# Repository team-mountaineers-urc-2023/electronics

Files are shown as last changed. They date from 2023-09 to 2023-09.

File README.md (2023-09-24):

# Electronics
This repository contains diagrams of Wanderer's electrical systems as well as PCBs designed by the Electronics sub-team.

# Table of Contents
[Downloading the Repository](#downloading-the-repository)   
[Required Software](#required-software)  
[Repository Contents](#repository-contents)  

# Downloading the Repository
## Pre-Install: SSH Key
An ssh key for your current machine must be added to your Github account to clone our repositories.  
SSH keys are used for passwordless authentication.  
For more information see https://docs.github.com/en/authentication/connecting-to-github-with-ssh.

## Creating an SSh Key
`$ ssh-keygen`  
Keep the default file name, add a password if you'd like. 

## Adding the SSH Key to your Github account
Go to https://github.com/settings/keys and click "New SSH Key"  
The title can be anything.  
For Key, copy paste the output of `$ cat ~/.ssh/id_rsa.pub`

## Clone the workspace
Install git if not done so already with `$ sudo apt install git` then:  
`git clone git@github.com:team-mountaineers-urc-2023/electronics.git ~electronics`
* If this is your first time talking to Github on your machine, you will receive a warning saying authenticity cannot be established.  
	Type "yes" and hit enter.

# Required Software
Block diagrams and schematics can be viewed using any PDF viewer.
All PCBs were designed using KiCad 7.0. The most recent version of the software can be downloaded at https://www.kicad.org/download/.

# Repository Contents

## System Schematics

Main Electronics Box Diagram

Manipulator Electronics Diagram

Science Electronics Diagram

## PCB Files

Battery Monitor v1.2

Payload PCB v3.1

Power Distribution Board

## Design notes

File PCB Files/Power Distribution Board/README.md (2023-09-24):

# Power Distribution Board

## Overview
The Power Distribution Board includes DC/DC converters used to step down the battery power to the necessary voltages needed throughout the rover. It can be populated with up to three 40 or 60W Traco Power DC/DC converters as well as two 20W regulators. It also includes integrated emergency stop circuitry and two pass-through power rails.

## Features
- 2-layer board
- Supports up to four batteries powering DC/DC converters
- Allows up to three 40W or 60W regulators
- Includes up to two 20W regulators
- Two pass-through voltage rails allowing unregulated power directly from batteries
- In-rush current limiters on drive motor connections
- Connectors have selectable outputs - jumpers determine which regulator they are attached to
- E-stop bypass allows the computer to remain powered when the emergency stop is used

## Contributors
- Scott Harper
- Conner Castle
- Yu Gu

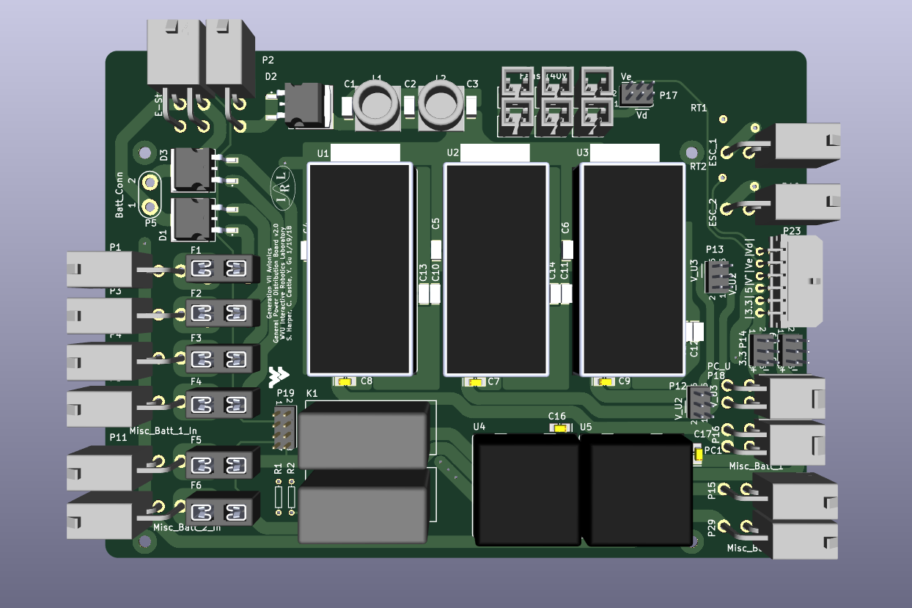
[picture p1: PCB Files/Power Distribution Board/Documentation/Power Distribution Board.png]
Picture of power distribution board


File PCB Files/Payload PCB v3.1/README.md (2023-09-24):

# Payload PCB v3.1

## Overview
The Payload PCB is used to control the electronics on the manipulator and the science payload. It can control up to eight DC motors and twelve servos. It also includes the hardware necessary for CAN bus communication, extra I/O connectors, payload select signals, and a USB2CAN converter.

## Features
- 4-layer board
- Raspberry Pi Pico microcontroller
- 4 DRV8874 H-bridge motor driver breakout boards capable of controlling 12V motors
- 2 TB6612FNG motor driver breakout boards that can each control two 12V motors or one stepper motor
- Capable of controlling up to twelve servo motors with selectable power output
- Hardware for CAN bus communication
- Optional place to put a 16th brick 12V regulator to power the board and payload motors
- 17 I/O connectors with GPIO, PWM, and/or analog input capabilities
- Payload select pins and LEDS to indicate which payload is plugged in
- Integrated USB2CAN converter which allows the computer to connect to the CAN bus using a USB connection
- Reverse polarity protection

## Contributors
- [Zach Waddell](https://github.com/zmw0006)

- [Ronald Butts](https://github.com/rmb0034)

- [Kendra Gillo](https://github.com/kgillo)

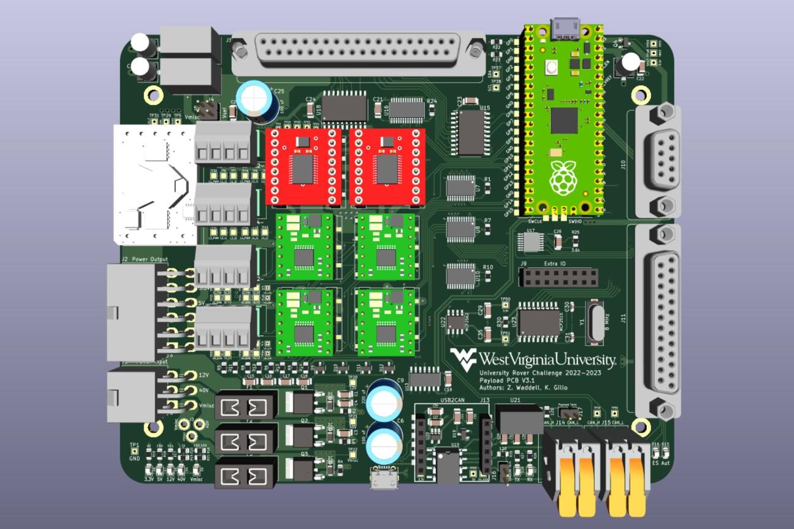
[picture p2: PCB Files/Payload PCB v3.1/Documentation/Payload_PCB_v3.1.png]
Picture of Payload PCB


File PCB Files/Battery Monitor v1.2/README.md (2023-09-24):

# Battery Monitor v1.2

## Overview
The battery monitor was designed for the 2023 rover to monitor its battery usage. The PCB features shunt resistors to measure the current draw from up to four batteries. It can communicate status using an LCD screen or over the rover's CAN bus.

## Features
- 4-layer board
- Raspberry Pi Pico microcontroller
- Measures battery voltage and current using shunt resistors combined with LTC4151 ICs
- Embedded emergency stop circuitry
- Ideal diode circuits to connect batteries in parallel
- Control for an external LCD screen and an LED strip
- Hardware for CAN bus communication
- Reverse polarity protection

## Contributors
- [Kendra Gillo](https://github.com/kgillo)

- [Zach Waddell](https://github.com/zmw0006)

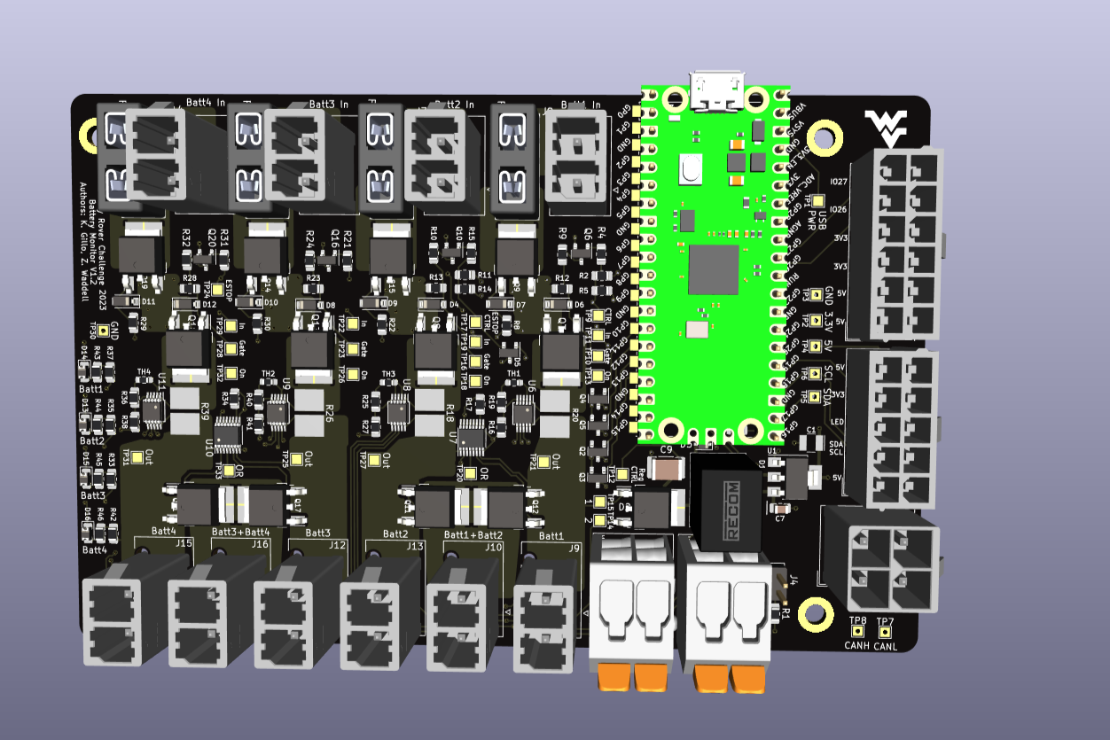
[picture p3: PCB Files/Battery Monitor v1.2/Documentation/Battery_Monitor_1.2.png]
Picture of Battery Monitor PCB


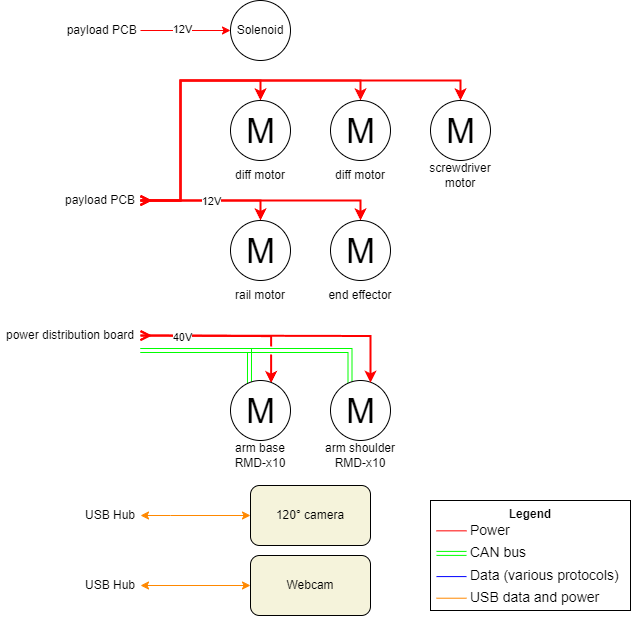
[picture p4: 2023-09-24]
System Schematics/Manipulator Electronics Diagram.png

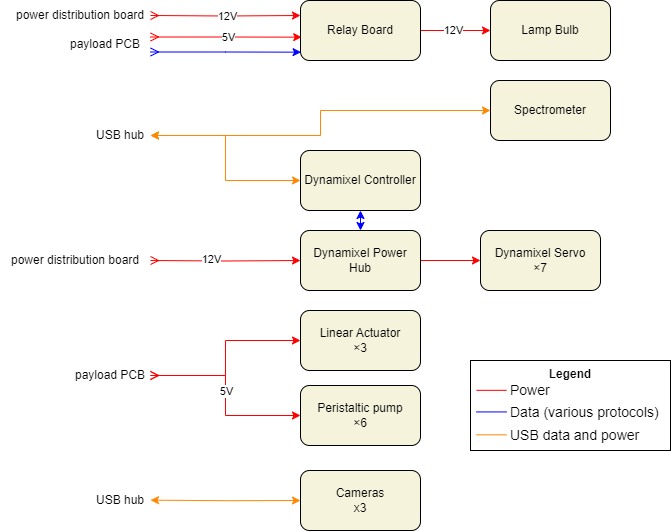
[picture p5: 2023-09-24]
System Schematics/Science Electronics Diagram.png

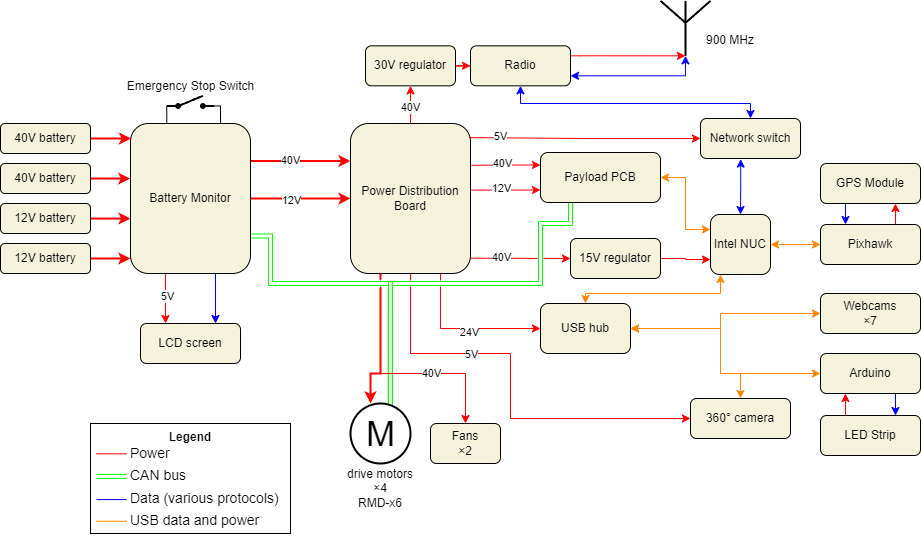
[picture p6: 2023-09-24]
System Schematics/Main Electronics Box Diagram.png

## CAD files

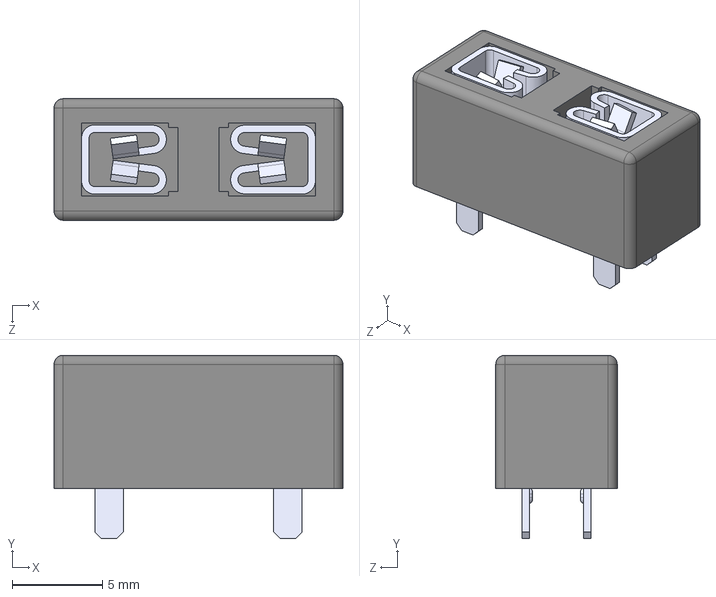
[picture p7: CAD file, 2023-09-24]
PCB Files/Battery Monitor v1.2/3D Models/3568.step
16.0 x 10.2 x 6.73 mm

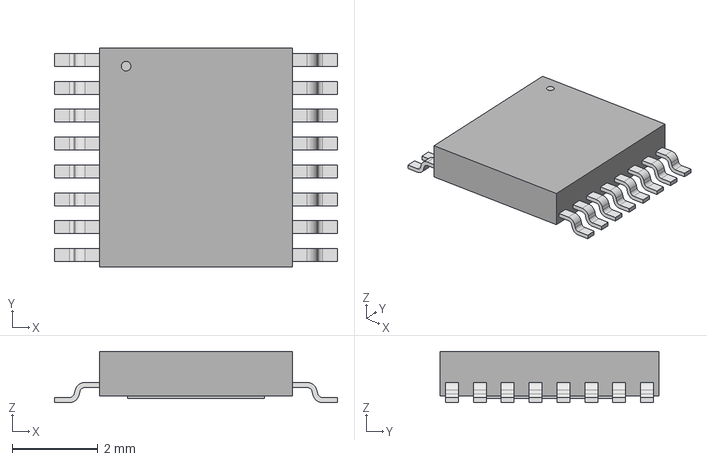
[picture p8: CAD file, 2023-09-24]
PCB Files/Payload PCB v3.1/3D Models/HTSSOP16_STM.step
6.60 x 5.11 x 1.20 mm

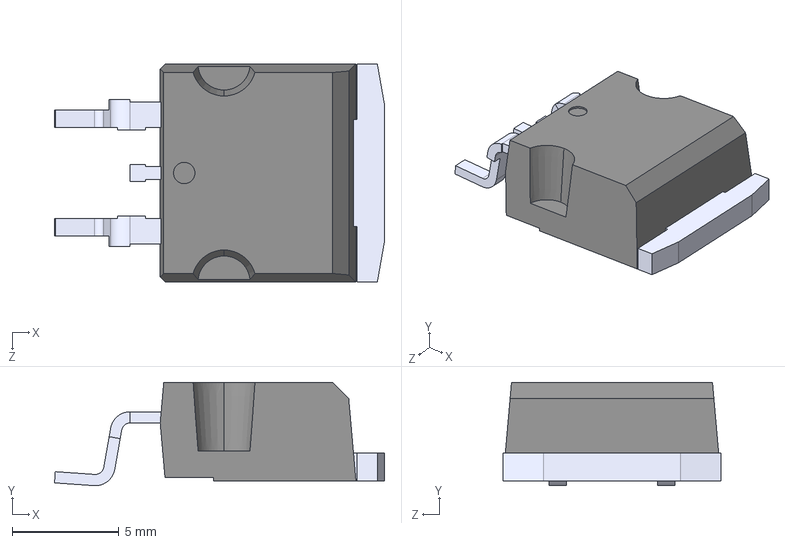
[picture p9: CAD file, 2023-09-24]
PCB Files/Power Distribution Board/3D Models/MBRB20200CTT4G.STEP
15.4 x 4.83 x 10.2 mm

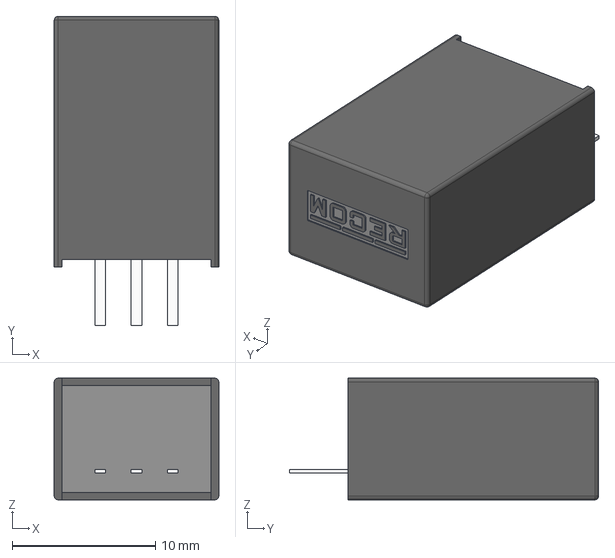
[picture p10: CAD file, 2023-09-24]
PCB Files/Battery Monitor v1.2/3D Models/R-78HB5.0-0.5.step
11.5 x 21.6 x 8.50 mm

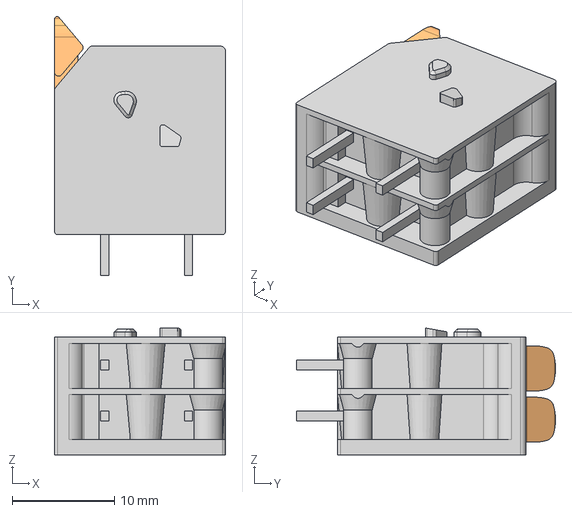
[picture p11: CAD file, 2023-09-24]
PCB Files/Battery Monitor v1.2/3D Models/2604-3102.stp
16.7 x 25.3 x 12.4 mm

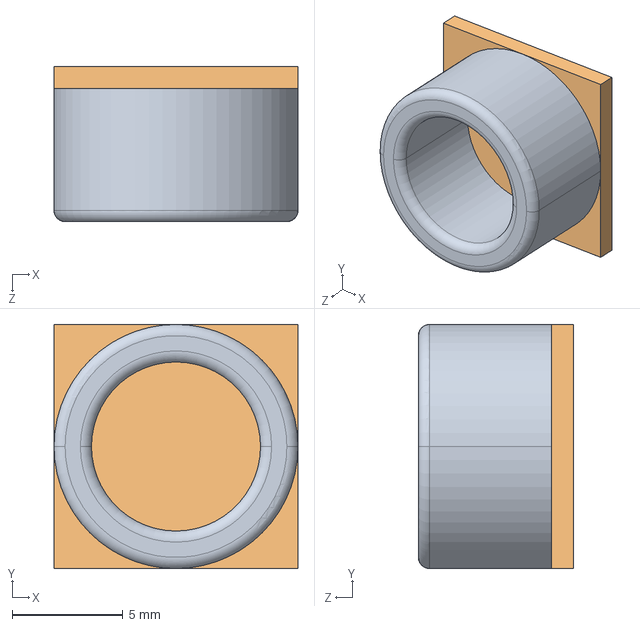
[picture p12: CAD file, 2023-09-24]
PCB Files/Power Distribution Board/3D Models/L1.STEP
11.0 x 11.0 x 7.00 mm
Cylinder.STEP
Extruded_14.STEP

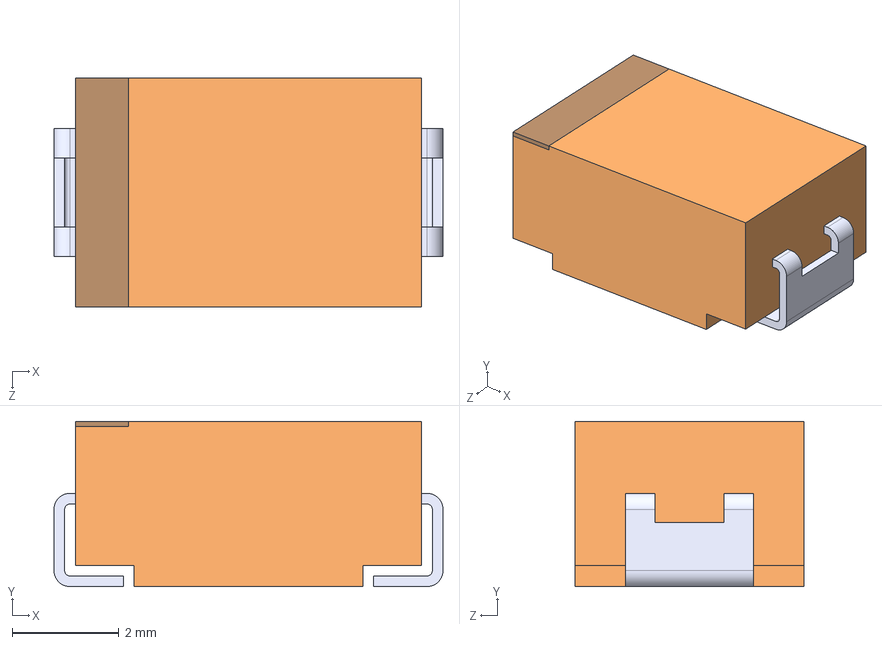
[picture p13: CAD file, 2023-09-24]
PCB Files/Battery Monitor v1.2/3D Models/2917.STEP
7.30 x 3.10 x 4.30 mm

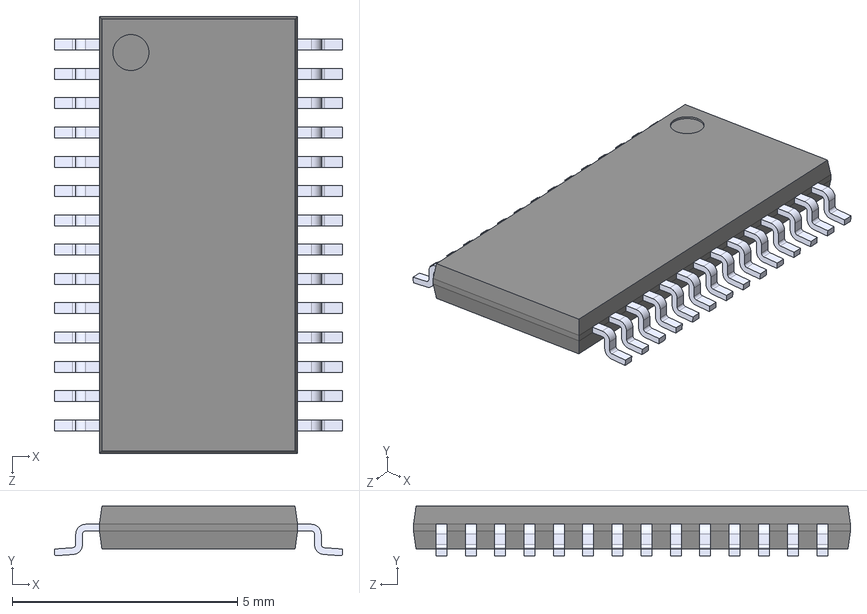
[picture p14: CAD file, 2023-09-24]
PCB Files/Payload PCB v3.1/3D Models/PCA9685PW_118.step
6.40 x 1.10 x 9.70 mm

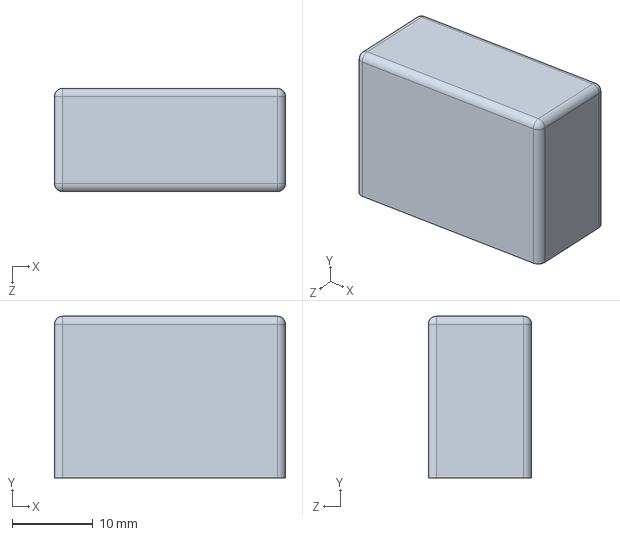
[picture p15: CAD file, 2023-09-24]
PCB Files/Power Distribution Board/3D Models/Relay.STEP
28.6 x 20.0 x 12.8 mm

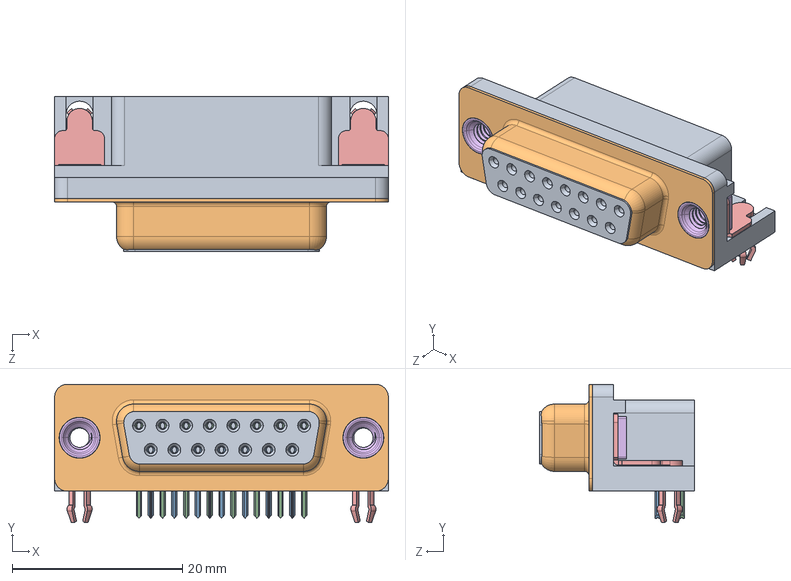
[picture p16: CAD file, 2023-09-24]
PCB Files/Payload PCB v3.1/3D Models/622-015-260-042 - EDAC D-Sub Connector.STEP
39.2 x 16.3 x 18.2 mm
622 Housing_15 Socket
622 Shell_15 Socket
622 Socket Bottom x 7
622 Contact Top x 8
622 4 Prong Board Lock x 2
622 4-40 Threaded Rivet x 2

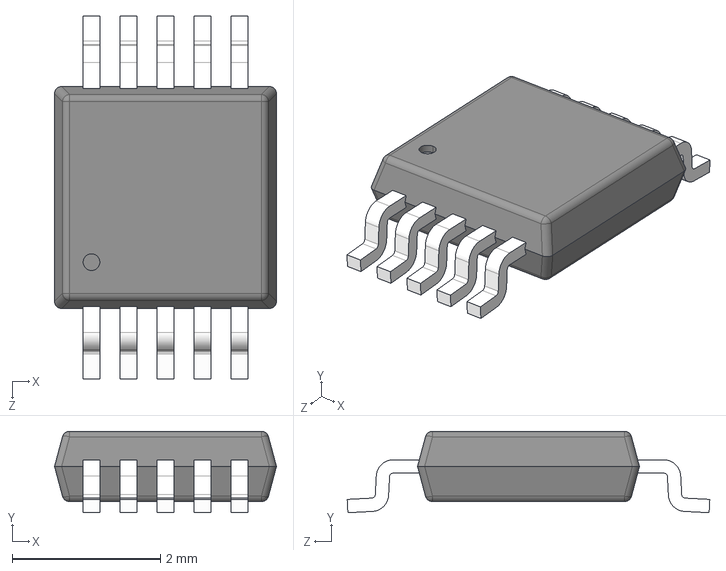
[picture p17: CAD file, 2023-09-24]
PCB Files/Battery Monitor v1.2/3D Models/MSOP-10.STEP
3.00 x 1.10 x 4.90 mm

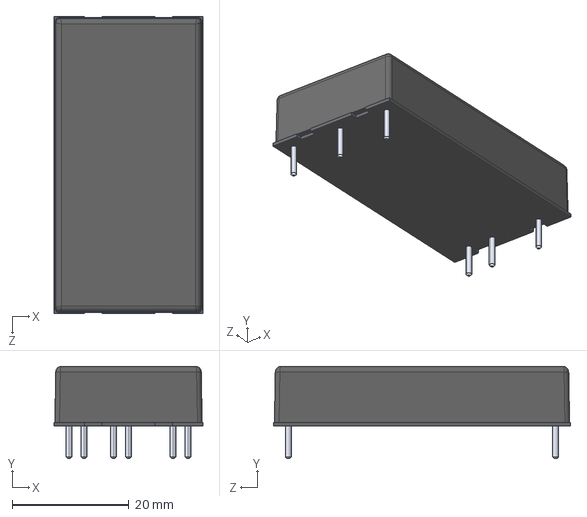
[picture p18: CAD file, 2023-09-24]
PCB Files/Power Distribution Board/3D Models/TEN 60-4813N.STEP
25.4 x 15.8 x 50.8 mm

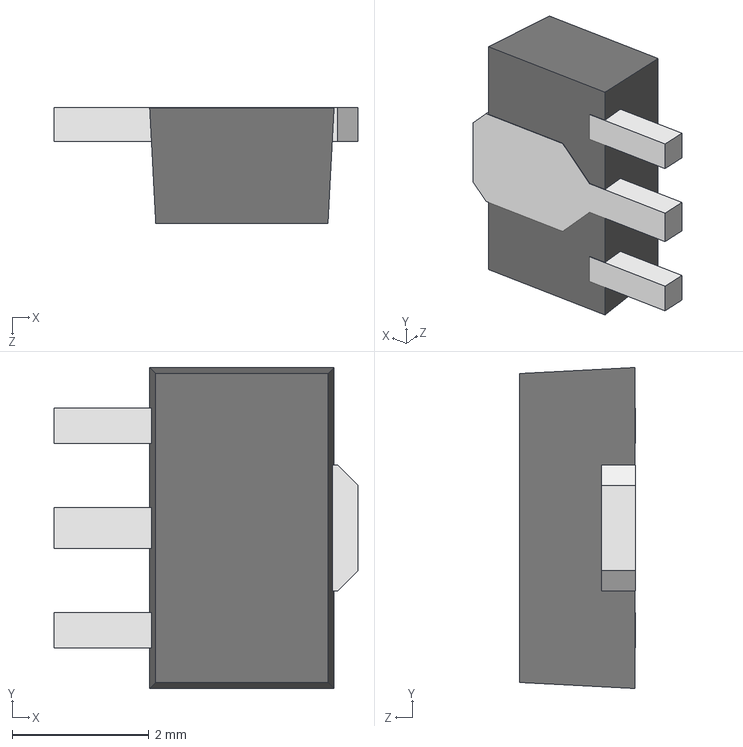
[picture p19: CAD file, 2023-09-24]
PCB Files/Battery Monitor v1.2/3D Models/TO-243AA.STEP
4.45 x 4.70 x 1.70 mm

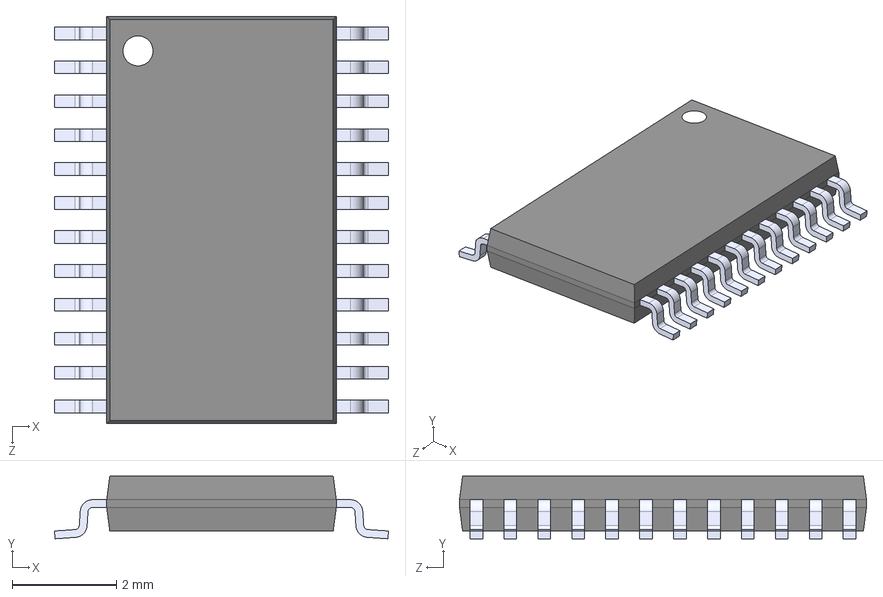
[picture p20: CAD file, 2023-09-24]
PCB Files/Payload PCB v3.1/3D Models/PCA9555PWR.step
6.40 x 1.20 x 7.80 mm

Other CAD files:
PCB Files/Power Distribution Board/3D Models/T491A474K025AT.STEP
PCB Files/Battery Monitor v1.2/3D Models/Molex 2x2.STEP
PCB Files/Payload PCB v3.1/3D Models/L77SDEH09SOL2RM8.stp
PCB Files/Battery Monitor v1.2/3D Models/VLS3015CX-680M-1.STEP
PCB Files/Battery Monitor v1.2/3D Models/039281103.stp
PCB Files/Battery Monitor v1.2/3D Models/039281123.stp
PCB Files/Battery Monitor v1.2/3D Models/768290102.step
PCB Files/Battery Monitor v1.2/3D Models/768290104.step
PCB Files/Battery Monitor v1.2/3D Models/Molex 2x1.STEP
PCB Files/Payload PCB v3.1/3D Models/050362296.stp
PCB Files/Payload PCB v3.1/3D Models/1050170001.stp
PCB Files/Payload PCB v3.1/3D Models/173010342_STP_173010342_rev1.stp
PCB Files/Payload PCB v3.1/3D Models/2604-1102.stp
PCB Files/Payload PCB v3.1/3D Models/2604-3104.stp
PCB Files/Payload PCB v3.1/3D Models/39301062.STEP
PCB Files/Payload PCB v3.1/3D Models/39301062.stp
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

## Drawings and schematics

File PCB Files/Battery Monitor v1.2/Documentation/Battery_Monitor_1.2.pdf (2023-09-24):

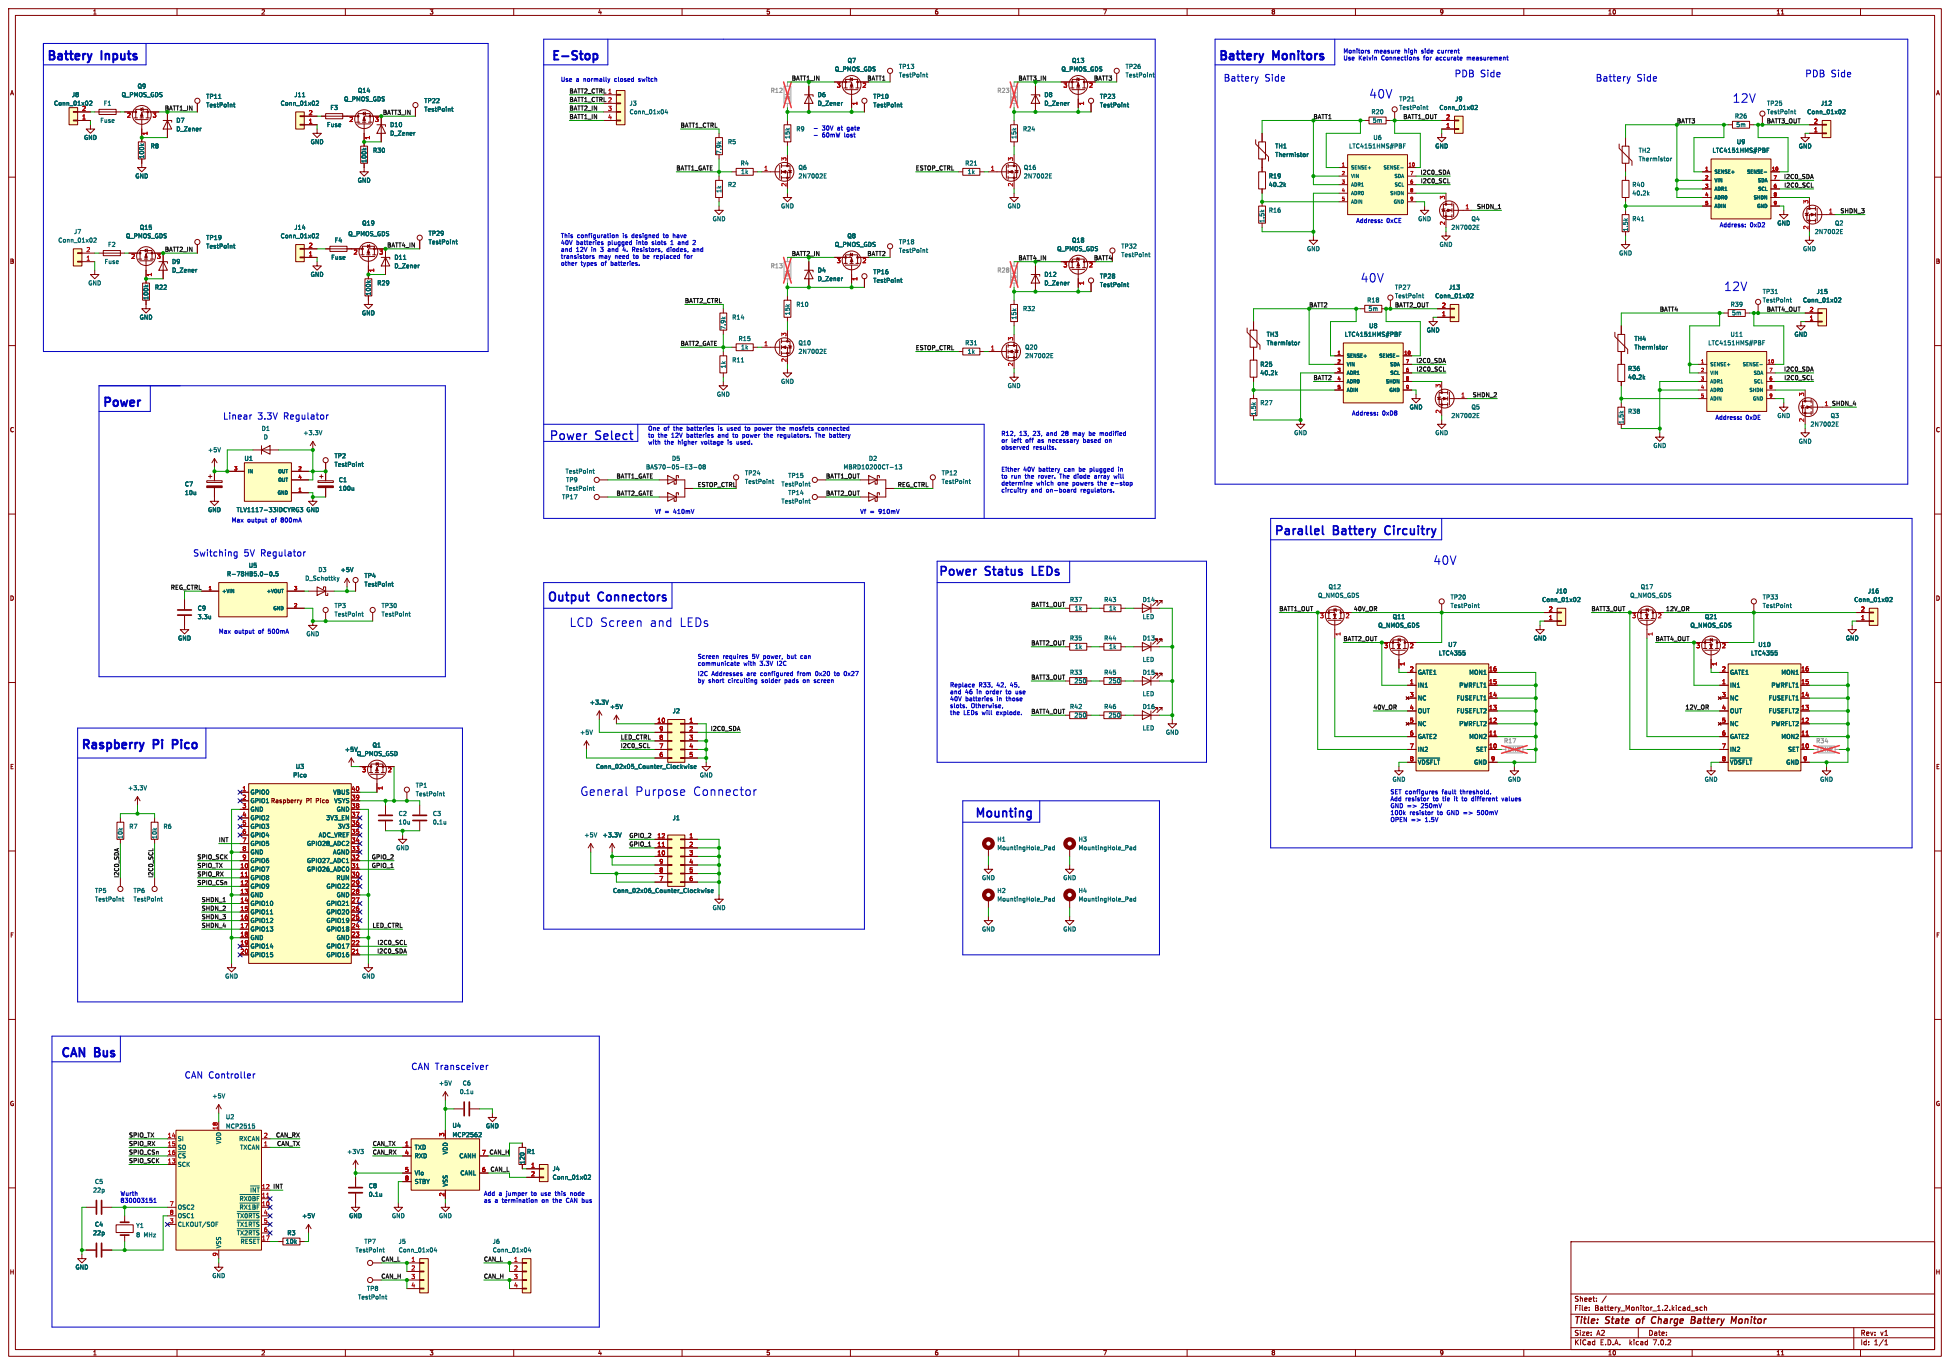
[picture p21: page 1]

PDB Side Battery Side

- 60mW lost Raspberry Pi Pico

R12, 13, 23, and 28 may be modified
or left off as necessary based on

Replace R33, 42, 45, and 46 in order to use

slots. Otherwise,
the LEDs will explode.

3 RXD 4 Vio 5 CANL 6 CANH 7 STBY 8 U4 MCP2562

3 RXD 4 Vio 5 CANL 6 CANH 7 STBY 8 GND

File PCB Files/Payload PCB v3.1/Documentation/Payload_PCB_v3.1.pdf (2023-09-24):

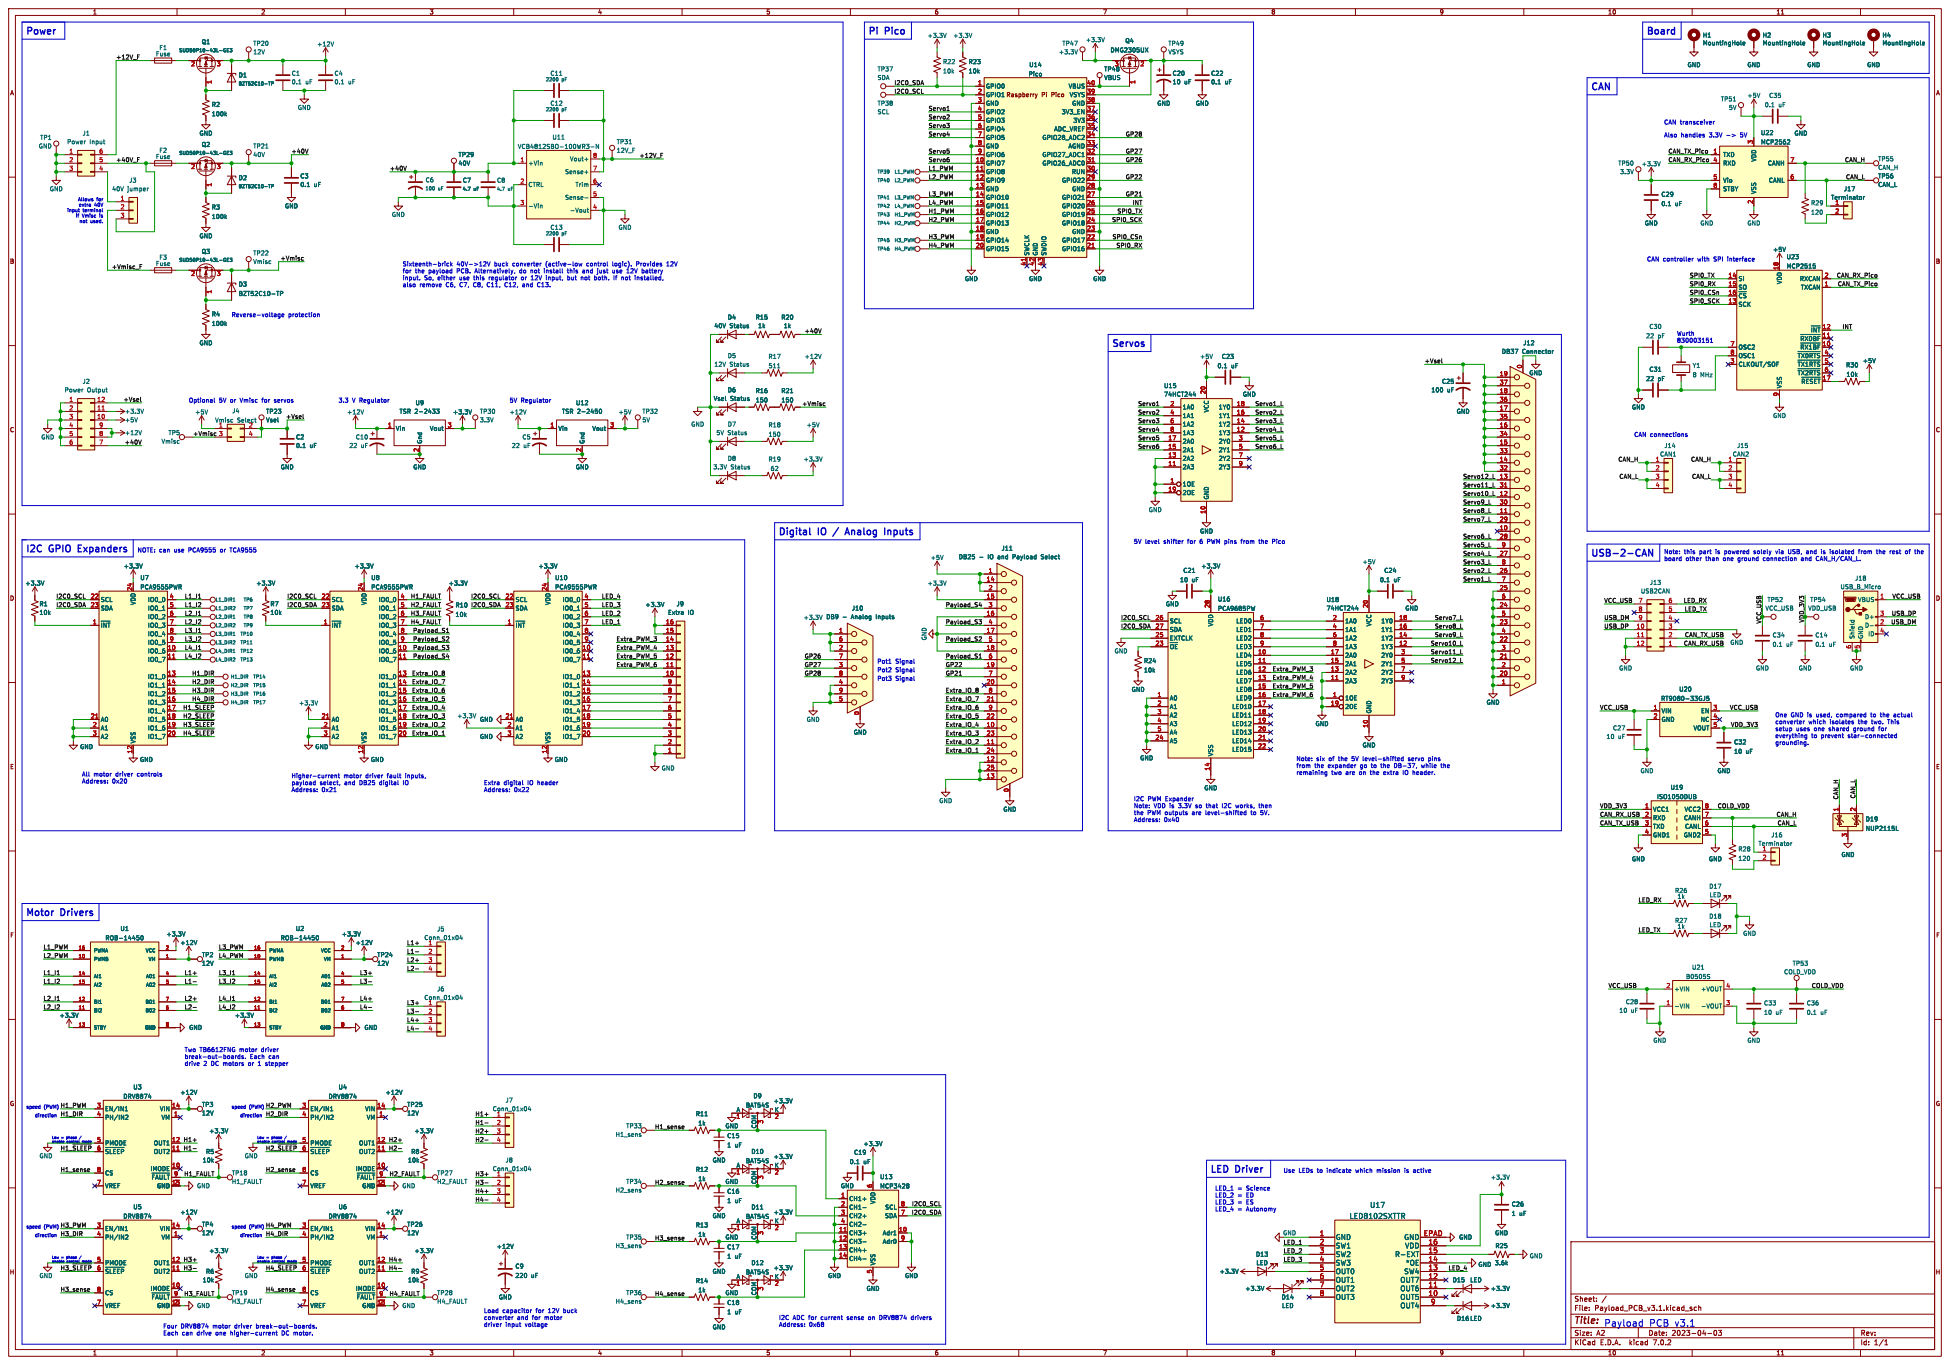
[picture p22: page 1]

input terminal
if Vmisc is not used.

J11 DB25 - IO and Payload Select 0

Digital IO / Analog Inputs

J11 DB25 - IO and Payload Select

All motor driver controls Address: 0x20

I2C PWM Expander Note: VDD is 3.3V so that I2C works, then

speed (PWM) speed (PWM) direction

6 SDA 7 SCL 8 Adr0 9 GNDGND GND

I2C ADC for current sense on DRV8874 drivers Address: 0x68

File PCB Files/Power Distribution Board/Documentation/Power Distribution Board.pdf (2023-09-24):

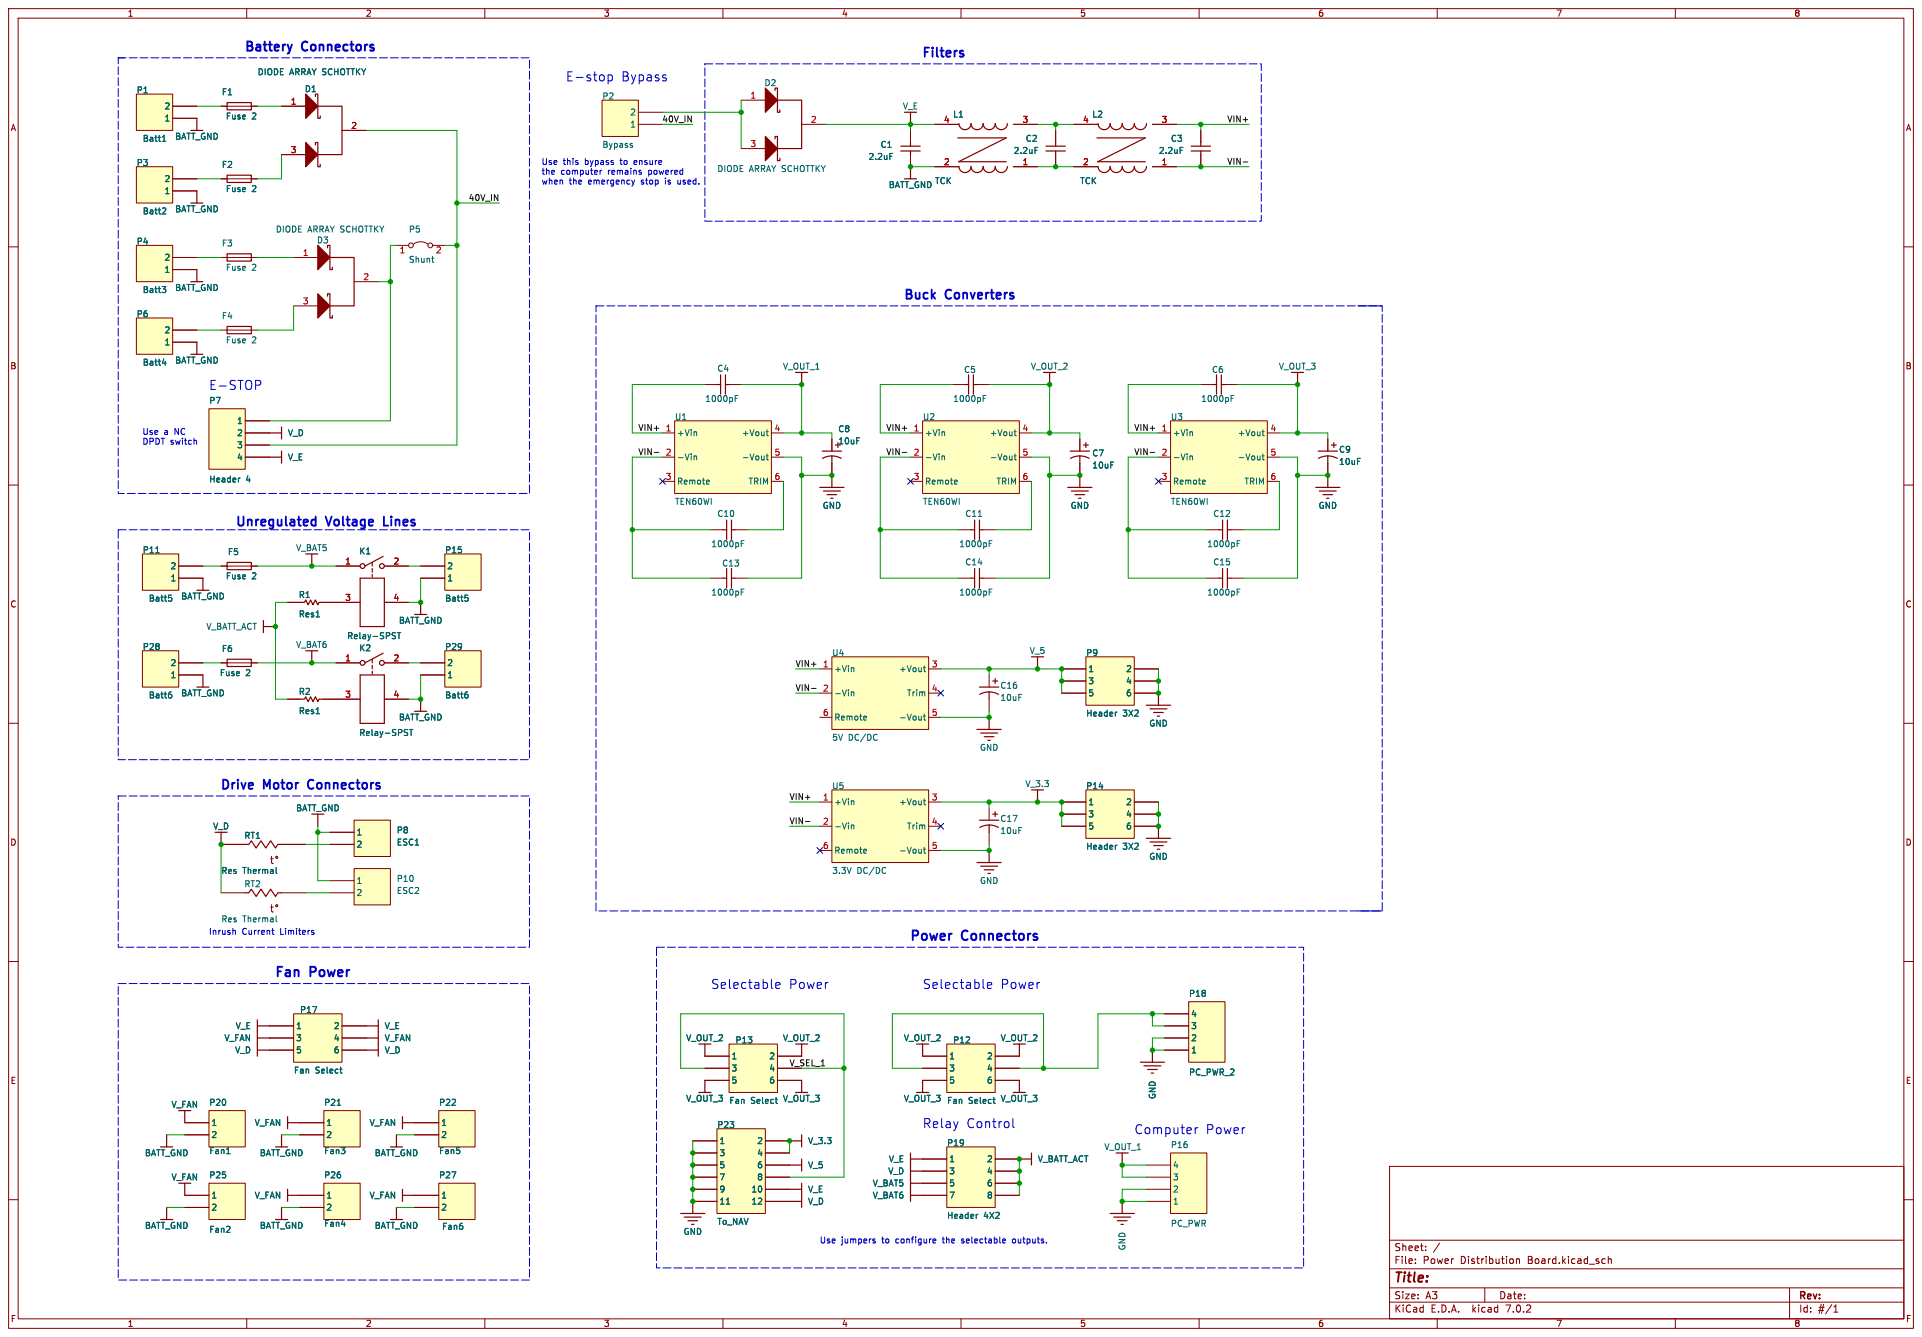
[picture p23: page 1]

Use this bypass to ensure

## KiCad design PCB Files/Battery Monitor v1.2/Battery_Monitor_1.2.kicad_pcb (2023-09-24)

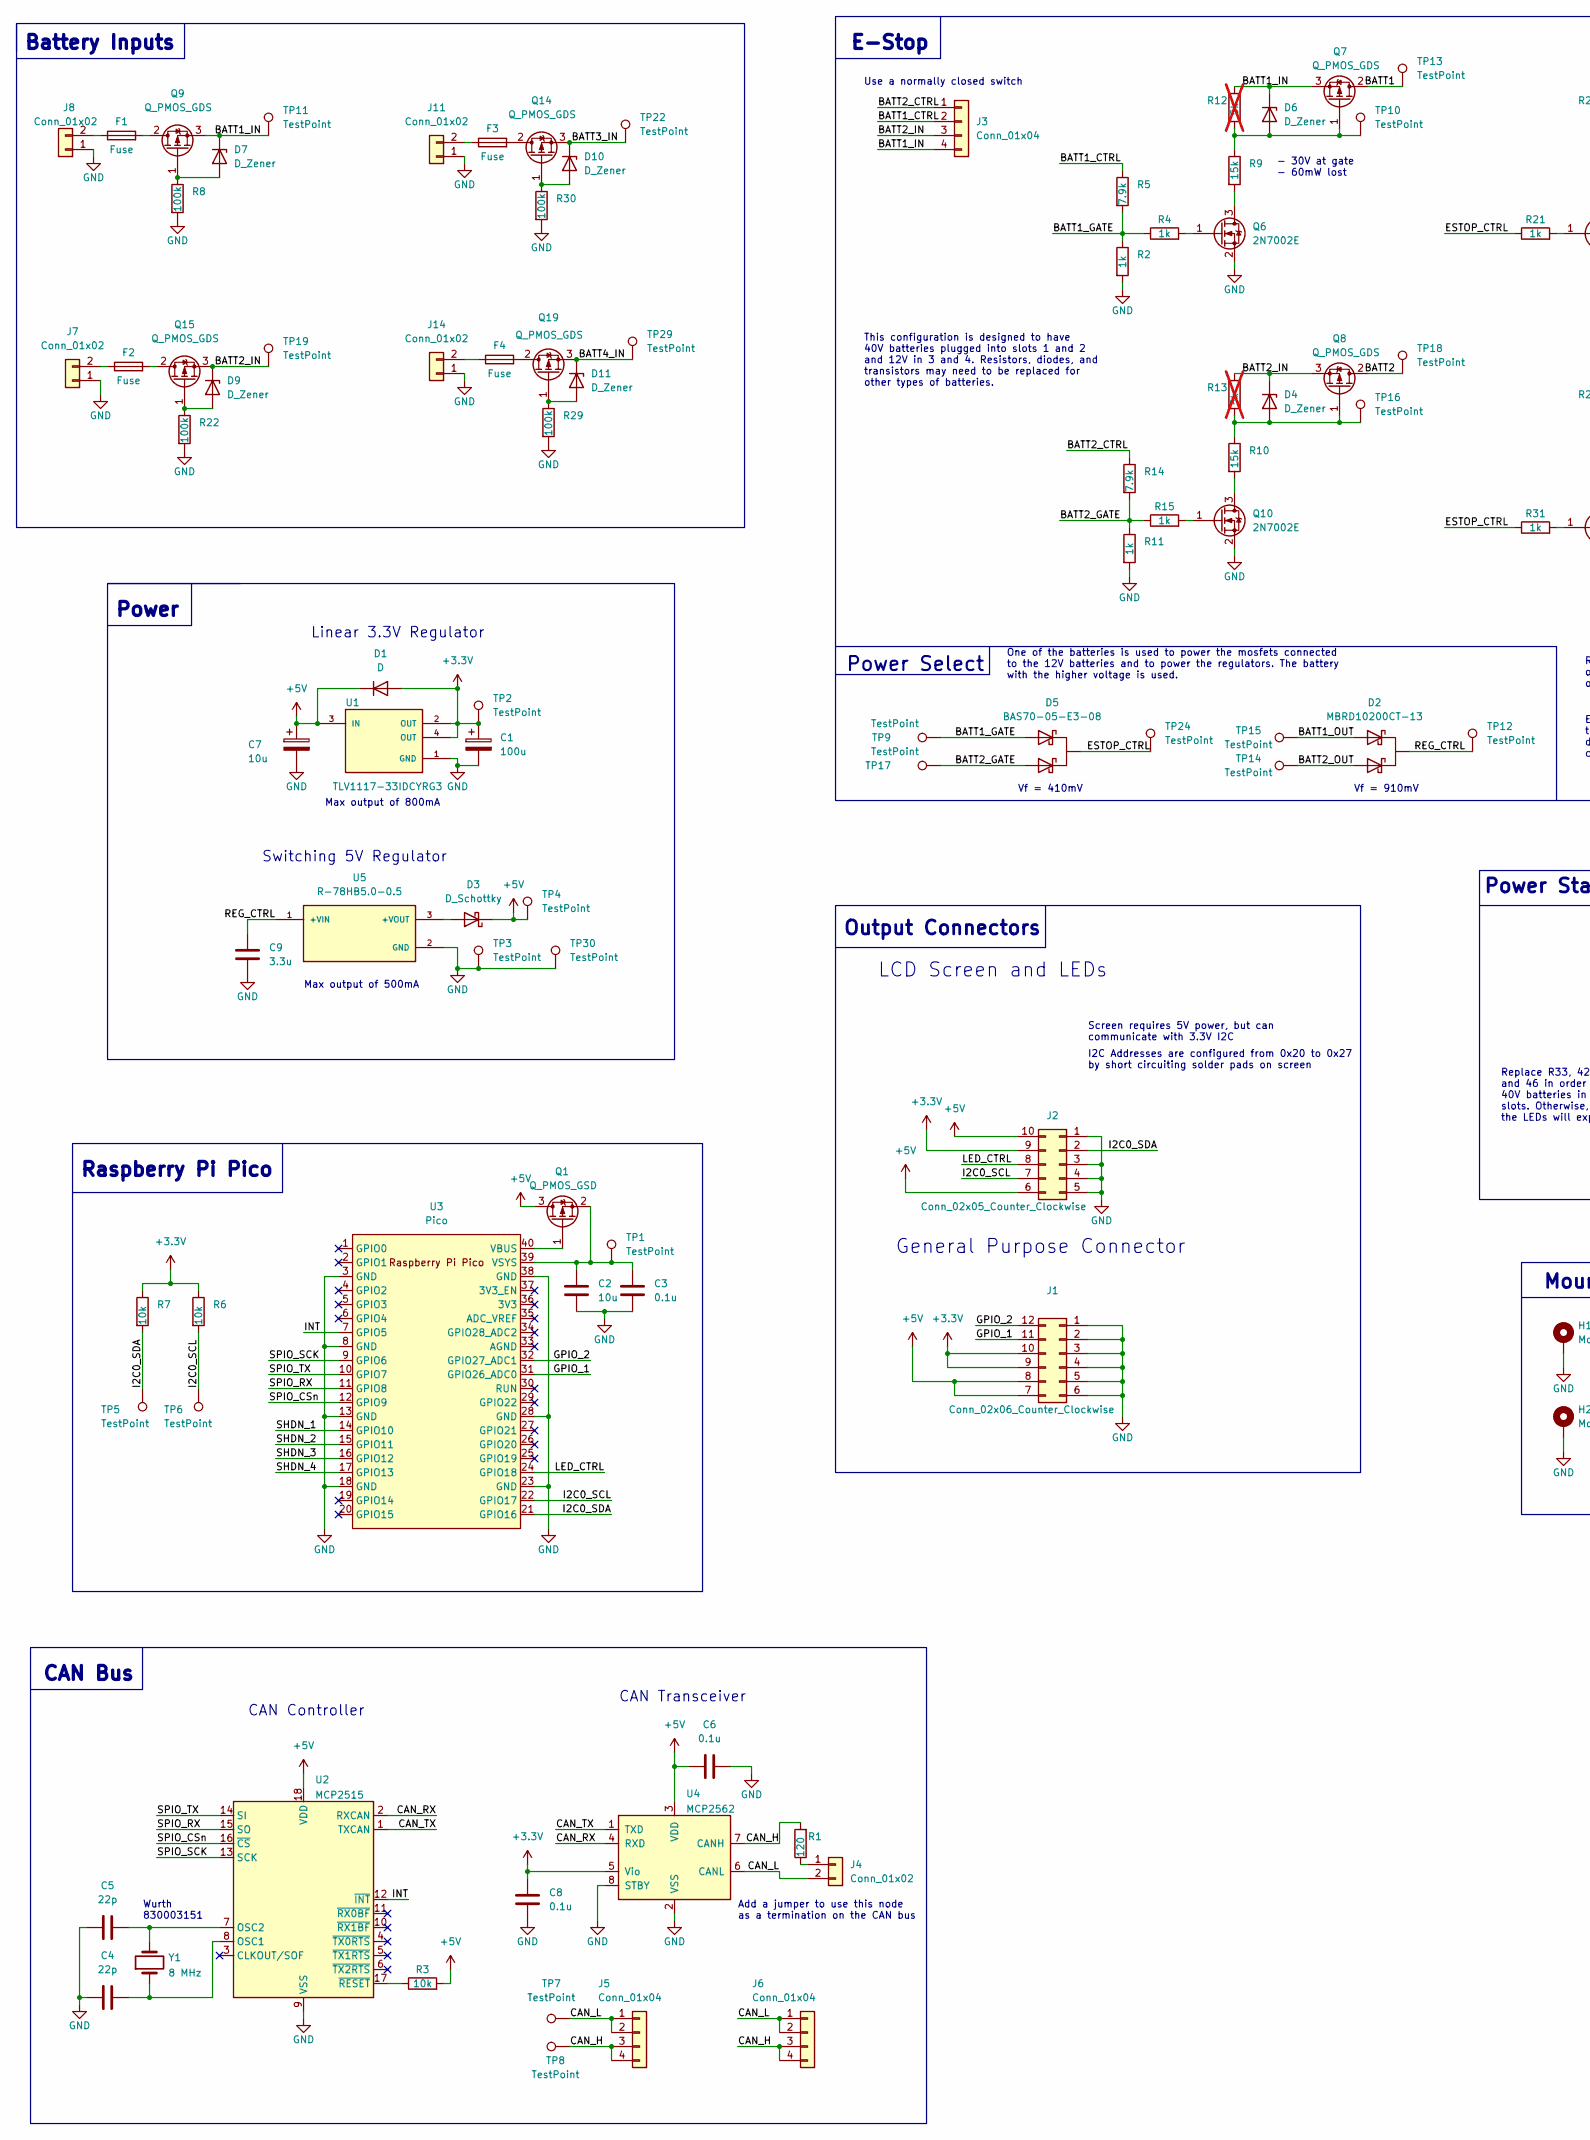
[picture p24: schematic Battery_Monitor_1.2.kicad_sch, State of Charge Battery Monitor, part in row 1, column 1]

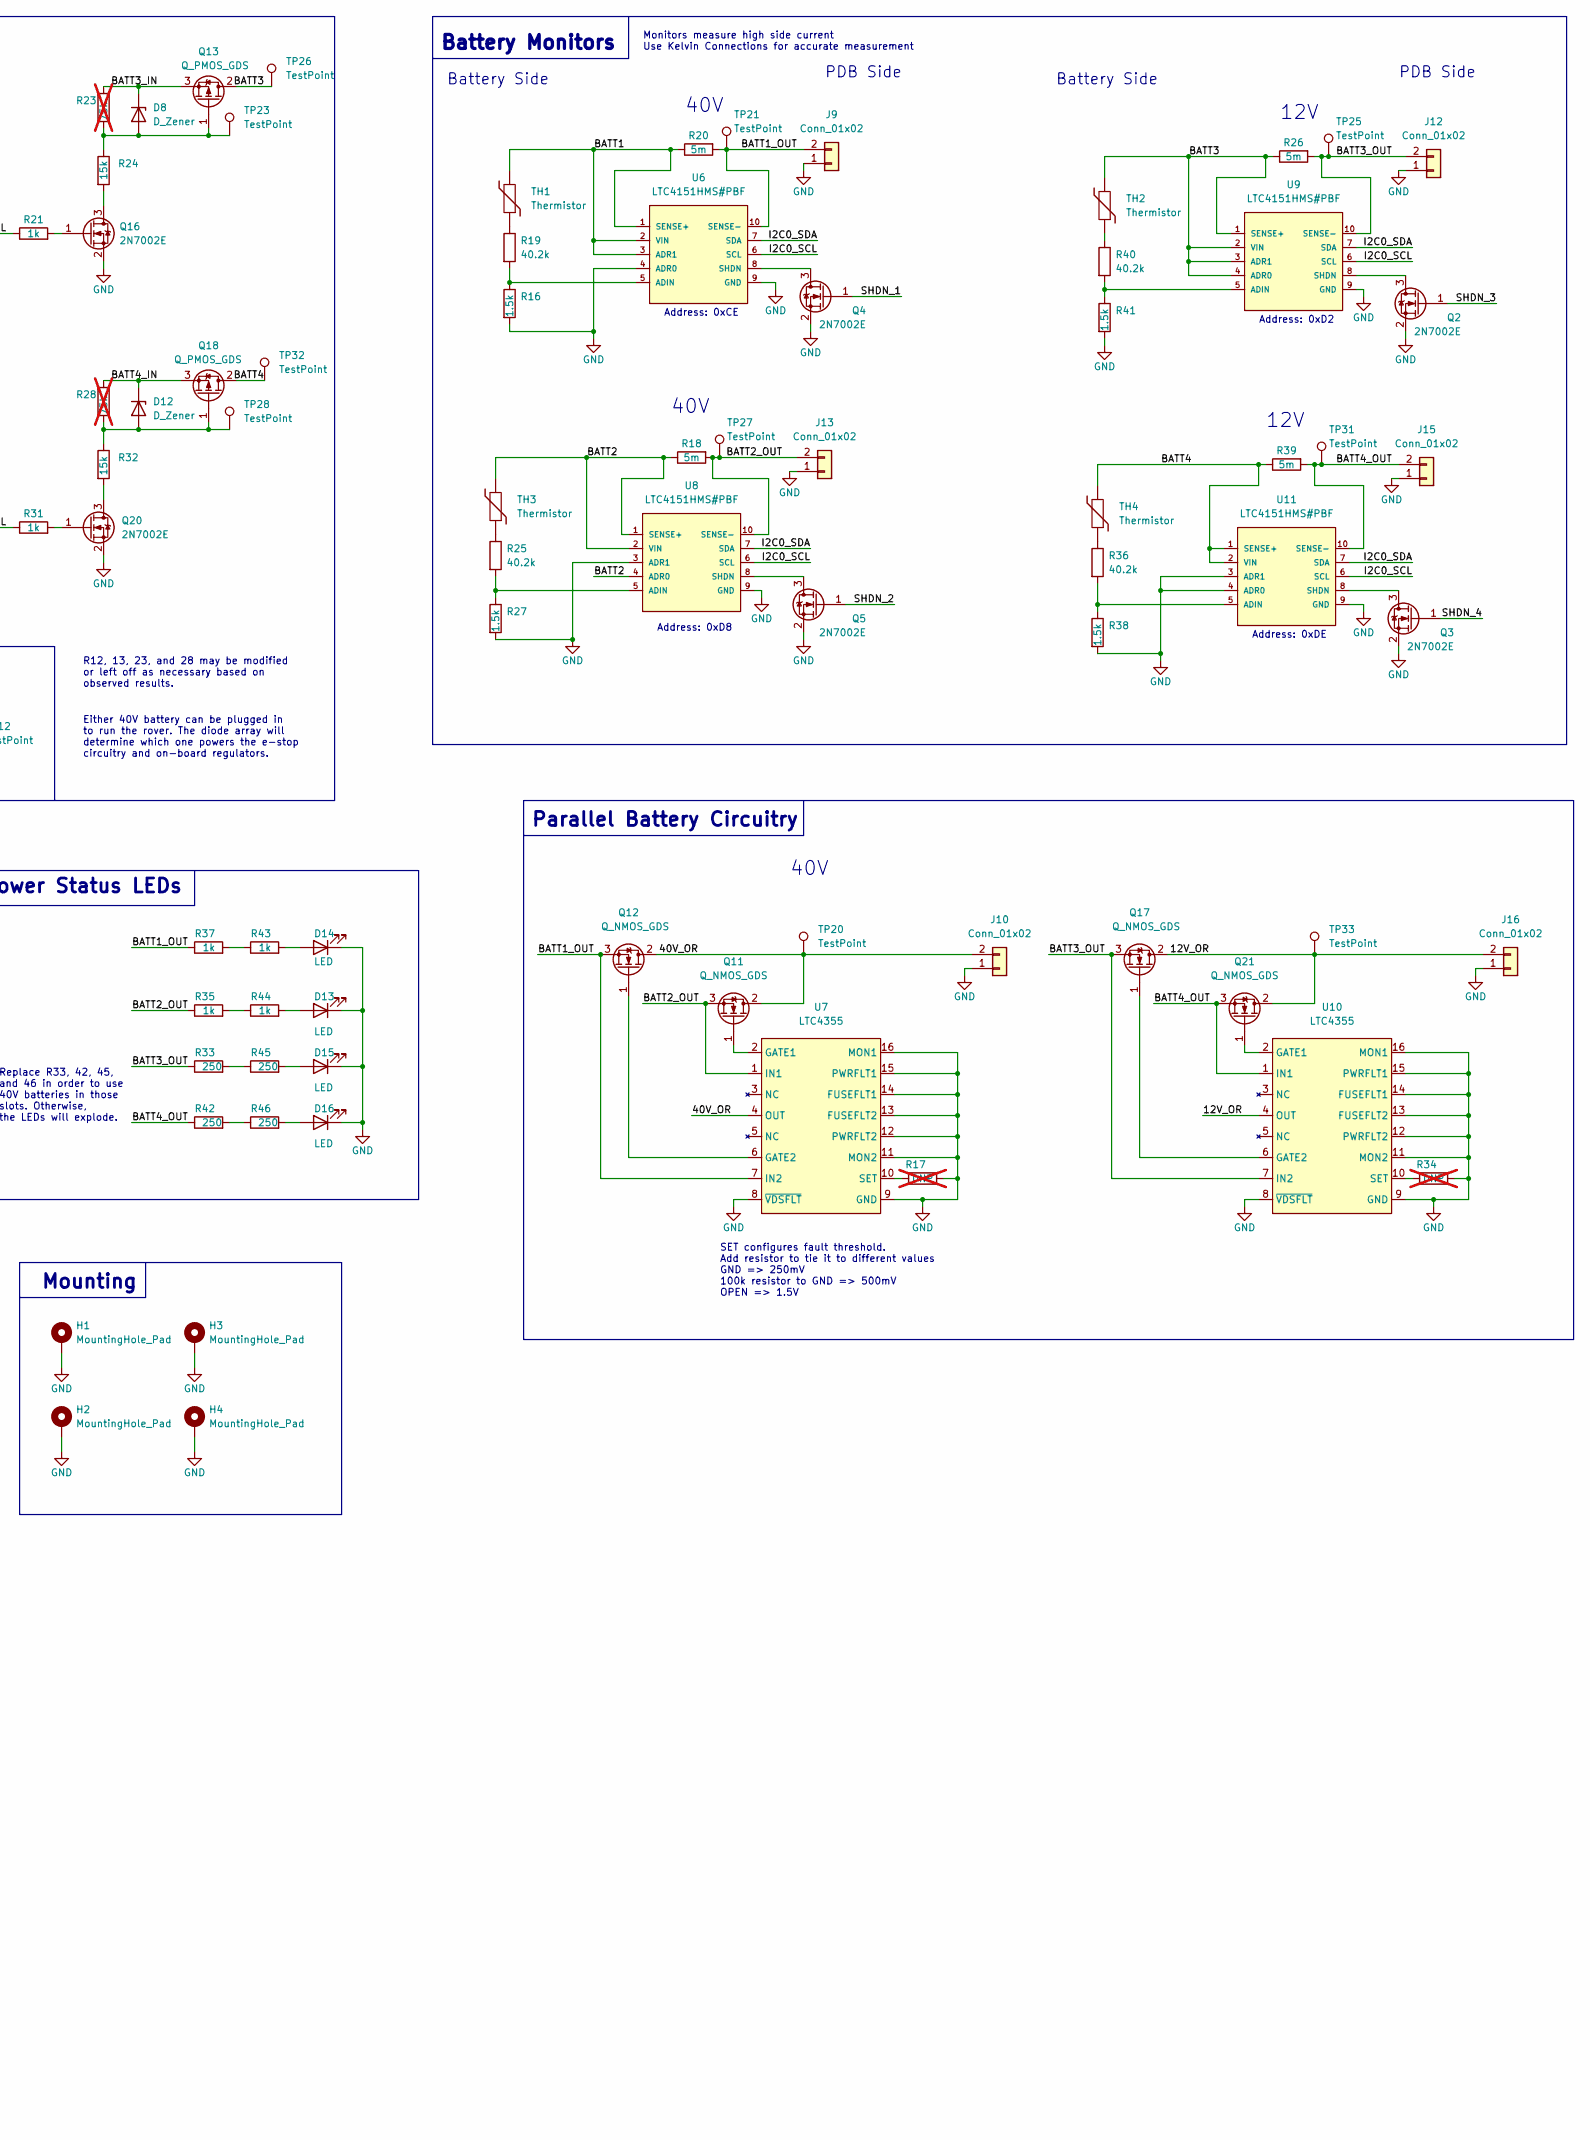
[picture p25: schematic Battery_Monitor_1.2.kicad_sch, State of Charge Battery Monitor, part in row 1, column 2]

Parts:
C1: 100u; 1411 (3528 Metric)
C2, C7: 10u; C_0805_2012Metric_Pad1.18x1.45mm_HandSolder
C3: 0.1u; C_1206_3216Metric_Pad1.33x1.80mm_HandSolder
C4, C5: 22p; C_0603_1608Metric_Pad1.08x0.95mm_HandSolder
C6, C8: 0.1u; C_1206_3216Metric_Pad1.33x1.80mm_HandSolder; MANUFACTURER_PART_NUMBER 1206B104J500CT
C9: 3.3u; C_1812_4532Metric_Pad1.57x3.40mm_HandSolder
D1: D; SOD123FL3; MANUFACTURER_PART_NUMBER GS1001FL_R1_00001
D2: MBRD10200CT-13; TO-252-2; MANUFACTURER_PART_NUMBER MBRD10200CT-13
D3: D_Schottky; D_SOD-323; MANUFACTURER_PART_NUMBER CUS08F30,H3F
D4, D6, D7, D8, D9, D10, D11, D12: D_Zener; D_SOD-123; MANUFACTURER_PART_NUMBER BZT52C10-TP
D5: BAS70-05-E3-08; SOT-23; MANUFACTURER_PART_NUMBER BAS70-05-E3-08
D13, D14, D15, D16: LED; D_0805_2012Metric_Pad1.15x1.40mm_HandSolder; MANUFACTURER_PART_NUMBER LTST-C171GKT
F1, F2, F3, F4: Fuse; FUSE_3568
H1, H2, H3, H4: MountingHole_Pad; MountingHole_3.2mm_M3_DIN965_Pad
J1: Conn_02x06_Counter_Clockwise; Molex_Mini-Fit_Jr_5566-12A_2x06_P4.20mm_Vertical; MANUFACTURER_PART_NUMBER 0039281123
J2: Conn_02x05_Counter_Clockwise; Molex_Mini-Fit_Jr_5566-10A_2x05_P4.20mm_Vertical
J3: Conn_01x04; Molex_Mega-Fit_76829-0104_2x02_P5.70mm_Vertical; MANUFACTURER_PART_NUMBER 76829-0104
J4: Conn_01x02; PinHeader_1x02_P2.54mm_Vertical
J5, J6: Conn_01x04; 2604-3102; MANUFACTURER_PART_NUMBER 2604-3102
J7, J8, J9, J10, J11, J12, J13, J14, J15, J16: Conn_01x02; MOLEX_768290102; MANUFACTURER_PART_NUMBER 768290102
Q1: Q_PMOS_GSD; SOT-23; MANUFACTURER_PART_NUMBER DMG2305UX-13
Q2, Q3, Q4, Q5, Q6, Q10, Q16, Q20: 2N7002E; SOT-23; MANUFACTURER_PART_NUMBER 2N7002E
Q7, Q8, Q9, Q13, Q14, Q15, Q18, Q19: Q_PMOS_GDS; TO-252-2; MANUFACTURER_PART_NUMBER SUD50P10-43L-GE3
Q11, Q12, Q17, Q21: Q_NMOS_GDS; TO-252-2; MANUFACTURER_PART_NUMBER FDD86367
R1: 120; R_0805_2012Metric_Pad1.20x1.40mm_HandSolder; MANUFACTURER_PART_NUMBER CFR25SJT-52-120R
R2, R4, R11, R15, R21, R31, R35, R37, R43, R44: 1k; R_0805_2012Metric_Pad1.20x1.40mm_HandSolder
R3, R6, R7: 10k; R_0805_2012Metric_Pad1.20x1.40mm_HandSolder; MANUFACTURER_PART_NUMBER RNCP0805FTD10K0
R5, R14: 7.9k; R_0805_2012Metric_Pad1.20x1.40mm_HandSolder
R8, R22, R29, R30: 100k; R_0805_2012Metric_Pad1.20x1.40mm_HandSolder
R9, R10, R24, R32: 15k; R_0805_2012Metric_Pad1.20x1.40mm_HandSolder
R12, R13: 5k; R_0805_2012Metric_Pad1.20x1.40mm_HandSolder; not fitted
R16, R27, R38, R41: 1.5k; R_0805_2012Metric_Pad1.20x1.40mm_HandSolder
R17, R34: DNP; R_0805_2012Metric_Pad1.20x1.40mm_HandSolder; not fitted
R18, R20, R26, R39: 5m; SMT-R005-1.0; MANUFACTURER_PART_NUMBER SMT-R005-1.0
R19, R25, R36, R40: 40.2k; R_0805_2012Metric_Pad1.20x1.40mm_HandSolder
R23, R28: 75k; R_0805_2012Metric_Pad1.20x1.40mm_HandSolder; not fitted
R33, R42, R45, R46: 250; R_0805_2012Metric_Pad1.20x1.40mm_HandSolder
TH1, TH2, TH3, TH4: Thermistor; R_0603_1608Metric_Pad0.98x0.95mm_HandSolder; MANUFACTURER_PART_NUMBER NTCS0603E3104GXT
TP1, TP9, TP10, TP11, TP12, TP13, TP14, TP15, TP16, TP17, TP18, TP19, TP20, TP21, TP22, TP23, TP24, TP25, TP26, TP27, TP28, TP29, TP31, TP32, TP33: TestPoint; TestPoint_Pad_1.5x1.5mm
TP2, TP3, TP4, TP5, TP6, TP7, TP8, TP30: TestPoint; TestPoint_THTPad_1.5x1.5mm_Drill0.7mm
U1: TLV1117-33IDCYRG3; SOT-223; MANUFACTURER_PART_NUMBER TLV1117-33IDCYRG3
U2: MCP2515; SOIC-18W_7.5x11.6mm_P1.27mm; MANUFACTURER_PART_NUMBER MCP2515
U3: Pico; RPi_Pico_SMD_TH; MANUFACTURER_PART_NUMBER SC0915
U4: MCP2562; SOIC-8_3.9x4.9mm_P1.27mm; MANUFACTURER_PART_NUMBER MCP2562
U5: R-78HB5.0-0.5; CONV_R-78HB5.0-0.5; MANUFACTURER_PART_NUMBER R-78HB5.0-0.5
U6, U8, U9, U11: LTC4151HMS#PBF; MSOP-10_3x3mm_P0.5mm; MANUFACTURER_PART_NUMBER LTC4151HMS#PBF
U7, U10: LTC4355; MSOP-16_3x4.039mm_P0.5mm; MANUFACTURER_PART_NUMBER LTC4355
Y1: 8 MHz; Crystal_SMD_HC49-SD; MANUFACTURER_PART_NUMBER 830003151

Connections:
+3.3V: C1.1, C8.1, D1.2 (A), J1.9, J1.10, J2.9, R6.1, R7.1, TP2.1, U1.2 (OUT), U1.4 (OUT), U4.5 (Vio)
+5V: C6.1, C7.1, D1.1 (K), D3.1 (K), J1.7, J1.8, J2.6, J2.10, Q1.3 (D), R3.2, TP4.1, U1.3 (IN), U2.18 (VDD), U4.3 (VDD)
/12V_OR: J16.2, Q17.2 (D), Q21.2 (D), TP33.1, U10.4 (OUT)
/40V_OR: J10.2, Q11.2 (D), Q12.2 (D), TP20.1, U7.4 (OUT)
/BATT1: Q7.2 (D), R20.1, TH1.2, TP13.1, U6.1 (SENSE+), U6.2 (VIN), U6.3 (ADR1)
/BATT1_CTRL: J3.2, R5.1
/BATT1_GATE: D5.1 (A), R2.1, R4.1, R5.2, TP9.1
/BATT1_IN: D6.1 (K), D7.1 (K), J3.4, Q7.3 (S), Q9.3 (S), R12.1, TP11.1
/BATT1_OUT: D2.1 (A), J9.2, Q12.3 (S), R20.2, R37.1, TP15.1, TP21.1, U6.10 (SENSE-), U7.7 (IN2)
/BATT2: Q8.2 (D), R18.1, TH3.2, TP18.1, U8.1 (SENSE+), U8.2 (VIN), U8.4 (ADR0)
/BATT2_CTRL: J3.1, R14.1
/BATT2_GATE: D5.2 (A), R11.1, R14.2, R15.1, TP17.1
/BATT2_IN: D4.1 (K), D9.1 (K), J3.3, Q8.3 (S), Q15.3 (S), R13.1, TP19.1
/BATT2_OUT: D2.3 (A), J13.2, Q11.3 (S), R18.2, R35.1, TP14.1, TP27.1, U7.1 (IN1), U8.10 (SENSE-)
/BATT3: Q13.2 (D), R26.1, TH2.2, TP26.1, U9.1 (SENSE+), U9.2 (VIN), U9.3 (ADR1), U9.4 (ADR0)
/BATT3_IN: D8.1 (K), D10.1 (K), Q13.3 (S), Q14.3 (S), R23.1, TP22.1
/BATT3_OUT: J12.2, Q17.3 (S), R26.2, R33.1, TP25.1, U9.10 (SENSE-), U10.7 (IN2)
/BATT4: Q18.2 (D), R39.1, TH4.2, TP32.1, U11.1 (SENSE+), U11.2 (VIN)
/BATT4_IN: D11.1 (K), D12.1 (K), Q18.3 (S), Q19.3 (S), R28.1, TP29.1
/BATT4_OUT: J15.2, Q21.3 (S), R39.2, R42.1, TP31.1, U10.1 (IN1), U11.10 (SENSE-)
/CAN_H: J5.3, J5.4, J6.3, J6.4, R1.2, TP8.1, U4.7 (CANH)
/CAN_L: J4.2, J5.1, J5.2, J6.1, J6.2, TP7.1, U4.6 (CANL)
/CAN_RX: U2.2 (RXCAN), U4.4 (RXD)
/CAN_TX: U2.1 (TXCAN), U4.1 (TXD)
/ESTOP_CTRL: D5.3 (K), R21.1, R31.1, TP24.1
/GPIO_1: J1.11, U3.31 (GPIO26_ADC0)
/GPIO_2: J1.12, U3.32 (GPIO27_ADC1)
/I2C0_SCL: J2.7, R6.2, TP6.1, U3.22 (GPIO17), U6.6 (SCL), U8.6 (SCL), U9.6 (SCL), U11.6 (SCL)
/I2C0_SDA: J2.2, R7.2, TP5.1, U3.21 (GPIO16), U6.7 (SDA), U8.7 (SDA), U9.7 (SDA), U11.7 (SDA)
/INT: U2.12 (~INT), U3.7 (GPIO5)
/LED_CTRL: J2.8, U3.24 (GPIO18)
/REG_CTRL: C9.1, D2.2 (K), TP12.1, U5.1 (+VIN)
/SHDN_1: Q4.1 (G), U3.14 (GPIO10)
/SHDN_2: Q5.1 (G), U3.15 (GPIO11)
/SHDN_3: Q2.1 (G), U3.16 (GPIO12)
/SHDN_4: Q3.1 (G), U3.17 (GPIO13)
/SPIO_CSn: U2.16 (~CS), U3.12 (GPIO9)
/SPIO_RX: U2.15 (SO), U3.11 (GPIO8)
/SPIO_SCK: U2.13 (SCK), U3.9 (GPIO6)
/SPIO_TX: U2.14 (SI), U3.10 (GPIO7)
GND: C1.2, C2.1, C3.1, C4.1, C5.1, C6.2, C7.2, C8.2, C9.2, D13.1 (K), D14.1 (K), D15.1 (K), D16.1 (K), H1.1, H2.1, H3.1, H4.1, J1.1, J1.2, J1.3, J1.4, J1.5, J1.6, J2.1, J2.3, J2.4, J2.5, J7.1, J8.1, J9.1, J10.1, J11.1, J12.1, J13.1, J14.1, J15.1, J16.1, Q2.2 (S), Q3.2 (S), Q4.2 (S), Q5.2 (S), Q6.2 (S), Q10.2 (S), Q16.2 (S), Q20.2 (S), R2.2, R8.2, R11.2, R16.2, R17.2, R22.2, R27.2, R29.2, R30.2, R34.2, R38.2, R41.2, TP3.1, TP30.1, U1.1 (GND), U2.9 (VSS), U3.3 (GND), U3.8 (GND), U3.13 (GND), U3.18 (GND), U3.23 (GND), U3.28 (GND), U3.38 (GND), U4.2 (VSS), U4.8 (STBY), U5.2 (GND), U6.4 (ADR0), U6.9 (GND), U7.8 (~VDSFLT), U7.9 (GND), U7.11 (MON2), U7.12 (PWRFLT2), U7.13 (FUSEFLT2), U7.14 (FUSEFLT1), U7.15 (PWRFLT1), U7.16 (MON1), U8.3 (ADR1), U8.9 (GND), U9.9 (GND), U10.8 (~VDSFLT), U10.9 (GND), U10.11 (MON2), U10.12 (PWRFLT2), U10.13 (FUSEFLT2), U10.14 (FUSEFLT1), U10.15 (PWRFLT1), U10.16 (MON1), U11.3 (ADR1), U11.4 (ADR0), U11.9 (GND)
unnamed: D3.2 (A), U5.3 (+VOUT)
unnamed: D4.2 (A), Q8.1 (G), R10.1, R13.2, TP16.1
unnamed: D6.2 (A), Q7.1 (G), R9.1, R12.2, TP10.1
unnamed: D7.2 (A), Q9.1 (G), R8.1
unnamed: D8.2 (A), Q13.1 (G), R23.2, R24.1, TP23.1
unnamed: D9.2 (A), Q15.1 (G), R22.1
unnamed: D10.2 (A), Q14.1 (G), R30.1
unnamed: D11.2 (A), Q19.1 (G), R29.1
unnamed: D12.2 (A), Q18.1 (G), R28.2, R32.1, TP28.1
unnamed: D13.2 (A), R44.2
unnamed: D14.2 (A), R43.2
unnamed: D15.2 (A), R45.2
unnamed: D16.2 (A), R46.2
unnamed: J4.1, R1.1
unnamed: F2.1, J7.2
unnamed: F1.1, J8.2
unnamed: F3.1, J11.2
unnamed: F4.1, J14.2
unnamed: Q1.1 (G), U3.40 (VBUS)
unnamed: C2.2, C3.2, Q1.2 (S), TP1.1, U3.39 (VSYS)
unnamed: Q2.3 (D), U9.8 (SHDN)
unnamed: Q3.3 (D), U11.8 (SHDN)
unnamed: Q4.3 (D), U6.8 (SHDN)
unnamed: Q5.3 (D), U8.8 (SHDN)
unnamed: Q6.3 (D), R9.2
unnamed: Q6.1 (G), R4.2
unnamed: F1.2, Q9.2 (D)
unnamed: Q10.3 (D), R10.2
unnamed: Q10.1 (G), R15.2
unnamed: Q11.1 (G), U7.2 (GATE1)
unnamed: Q12.1 (G), U7.6 (GATE2)
unnamed: F3.2, Q14.2 (D)
unnamed: F2.2, Q15.2 (D)
unnamed: Q16.3 (D), R24.2
unnamed: Q16.1 (G), R21.2
unnamed: Q17.1 (G), U10.6 (GATE2)
unnamed: F4.2, Q19.2 (D)
unnamed: Q20.3 (D), R32.2
unnamed: Q20.1 (G), R31.2
unnamed: Q21.1 (G), U10.2 (GATE1)
unnamed: R19.1, TH1.1
unnamed: R25.1, TH3.1
unnamed: R33.2, R45.1
unnamed: R35.2, R44.1
unnamed: R36.1, TH4.1
unnamed: R37.2, R43.1
unnamed: R40.1, TH2.1
unnamed: R42.2, R46.1
unnamed: C4.2, U2.8 (OSC1), Y1.1
unnamed: C5.2, U2.7 (OSC2), Y1.2
unnamed: R3.1, U2.17 (~RESET)
unnamed: R16.1, R19.2, U6.5 (ADIN)
unnamed: R17.1, U7.10 (SET)
unnamed: R25.2, R27.1, U8.5 (ADIN)
unnamed: R40.2, R41.1, U9.5 (ADIN)
unnamed: R34.1, U10.10 (SET)
unnamed: R36.2, R38.1, U11.5 (ADIN)

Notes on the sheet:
One of the batteries is used to power the mosfets connected to the 12V batteries and to power the regulators. The battery with the higher voltage is used.
Either 40V battery can be plugged in to run the rover. The diode array will determine which one powers the e-stop circuitry and on-board regulators.
40V
- 30V at gate - 60mW lost
SET configures fault threshold. Add resistor to tie it to different values GND => 250mV 100k resistor to GND => 500mV OPEN => 1.5V
Wurth 830003151
Power
CAN Transceiver
Replace R33, 42, 45, and 46 in order to use 40V batteries in those slots. Otherwise, the LEDs will explode.
Address: 0xD8
Address: 0xD2
Power Select
CAN Bus
This configuration is designed to have 40V batteries plugged into slots 1 and 2 and 12V in 3 and 4. Resistors, diodes, and transistors may need to be replaced for other types of batteries.
Max output of 500mA
Max output of 800mA
Add a jumper to use this node as a termination on the CAN bus
Address: 0xDE
Mounting
12V
Parallel Battery Circuitry
PDB Side
Raspberry Pi Pico
CAN Controller
Power Status LEDs
LCD Screen and LEDs
R12, 13, 23, and 28 may be modified or left off as necessary based on observed results.
Vf = 910mV
Monitors measure high side current Use Kelvin Connections for accurate measurement
I2C Addresses are configured from 0x20 to 0x27 by short circuiting solder pads on screen
Battery Side
Use a normally closed switch
Battery Inputs
Battery Monitors
E-Stop
Linear 3.3V Regulator
Screen requires 5V power, but can communicate with 3.3V I2C
Address: 0xCE
Vf = 410mV
General Purpose Connector

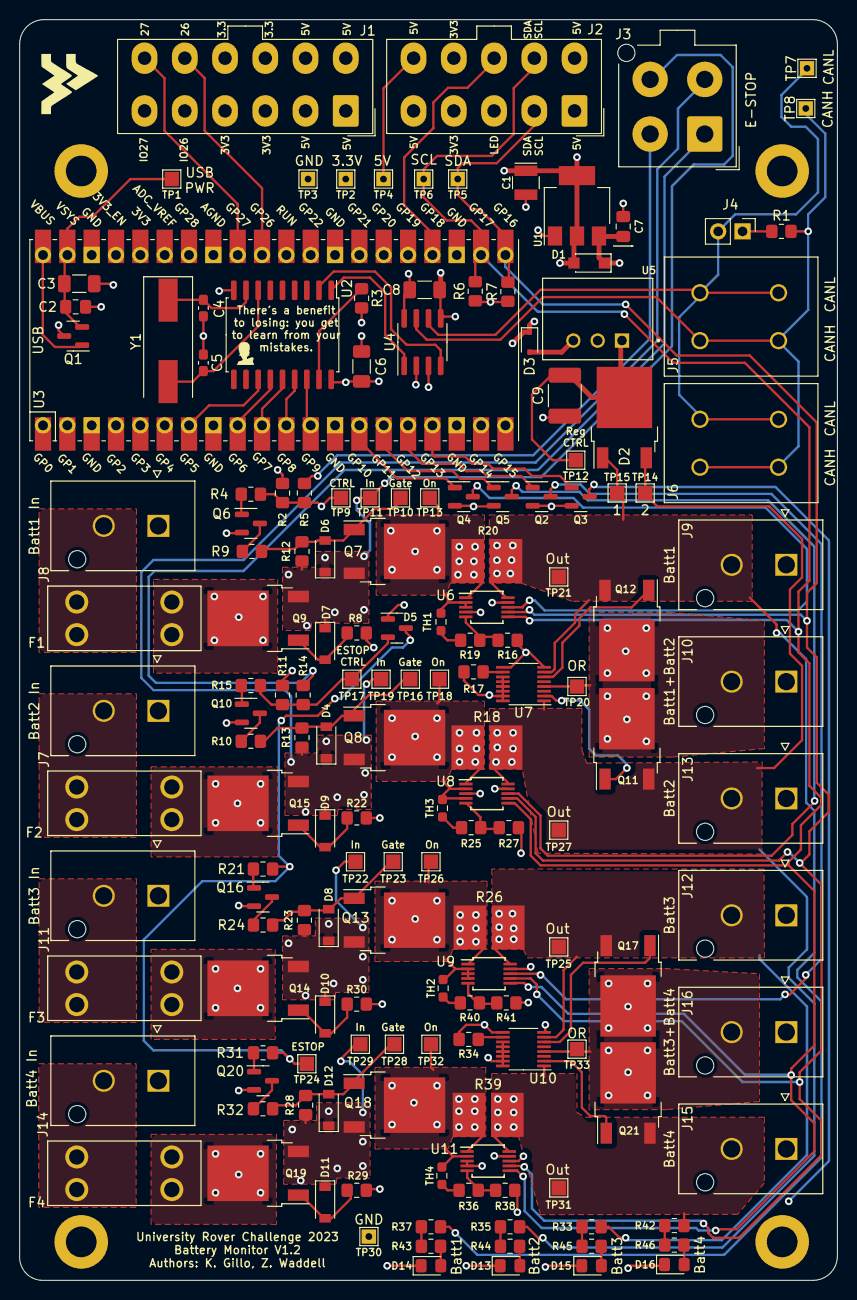
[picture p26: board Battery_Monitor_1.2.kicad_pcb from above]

Board: 4 copper layers, 85.3 x 131.6 mm, 166 parts (0 on the bottom side), 98 nets.

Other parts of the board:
G1: LOGO; Flying_WV

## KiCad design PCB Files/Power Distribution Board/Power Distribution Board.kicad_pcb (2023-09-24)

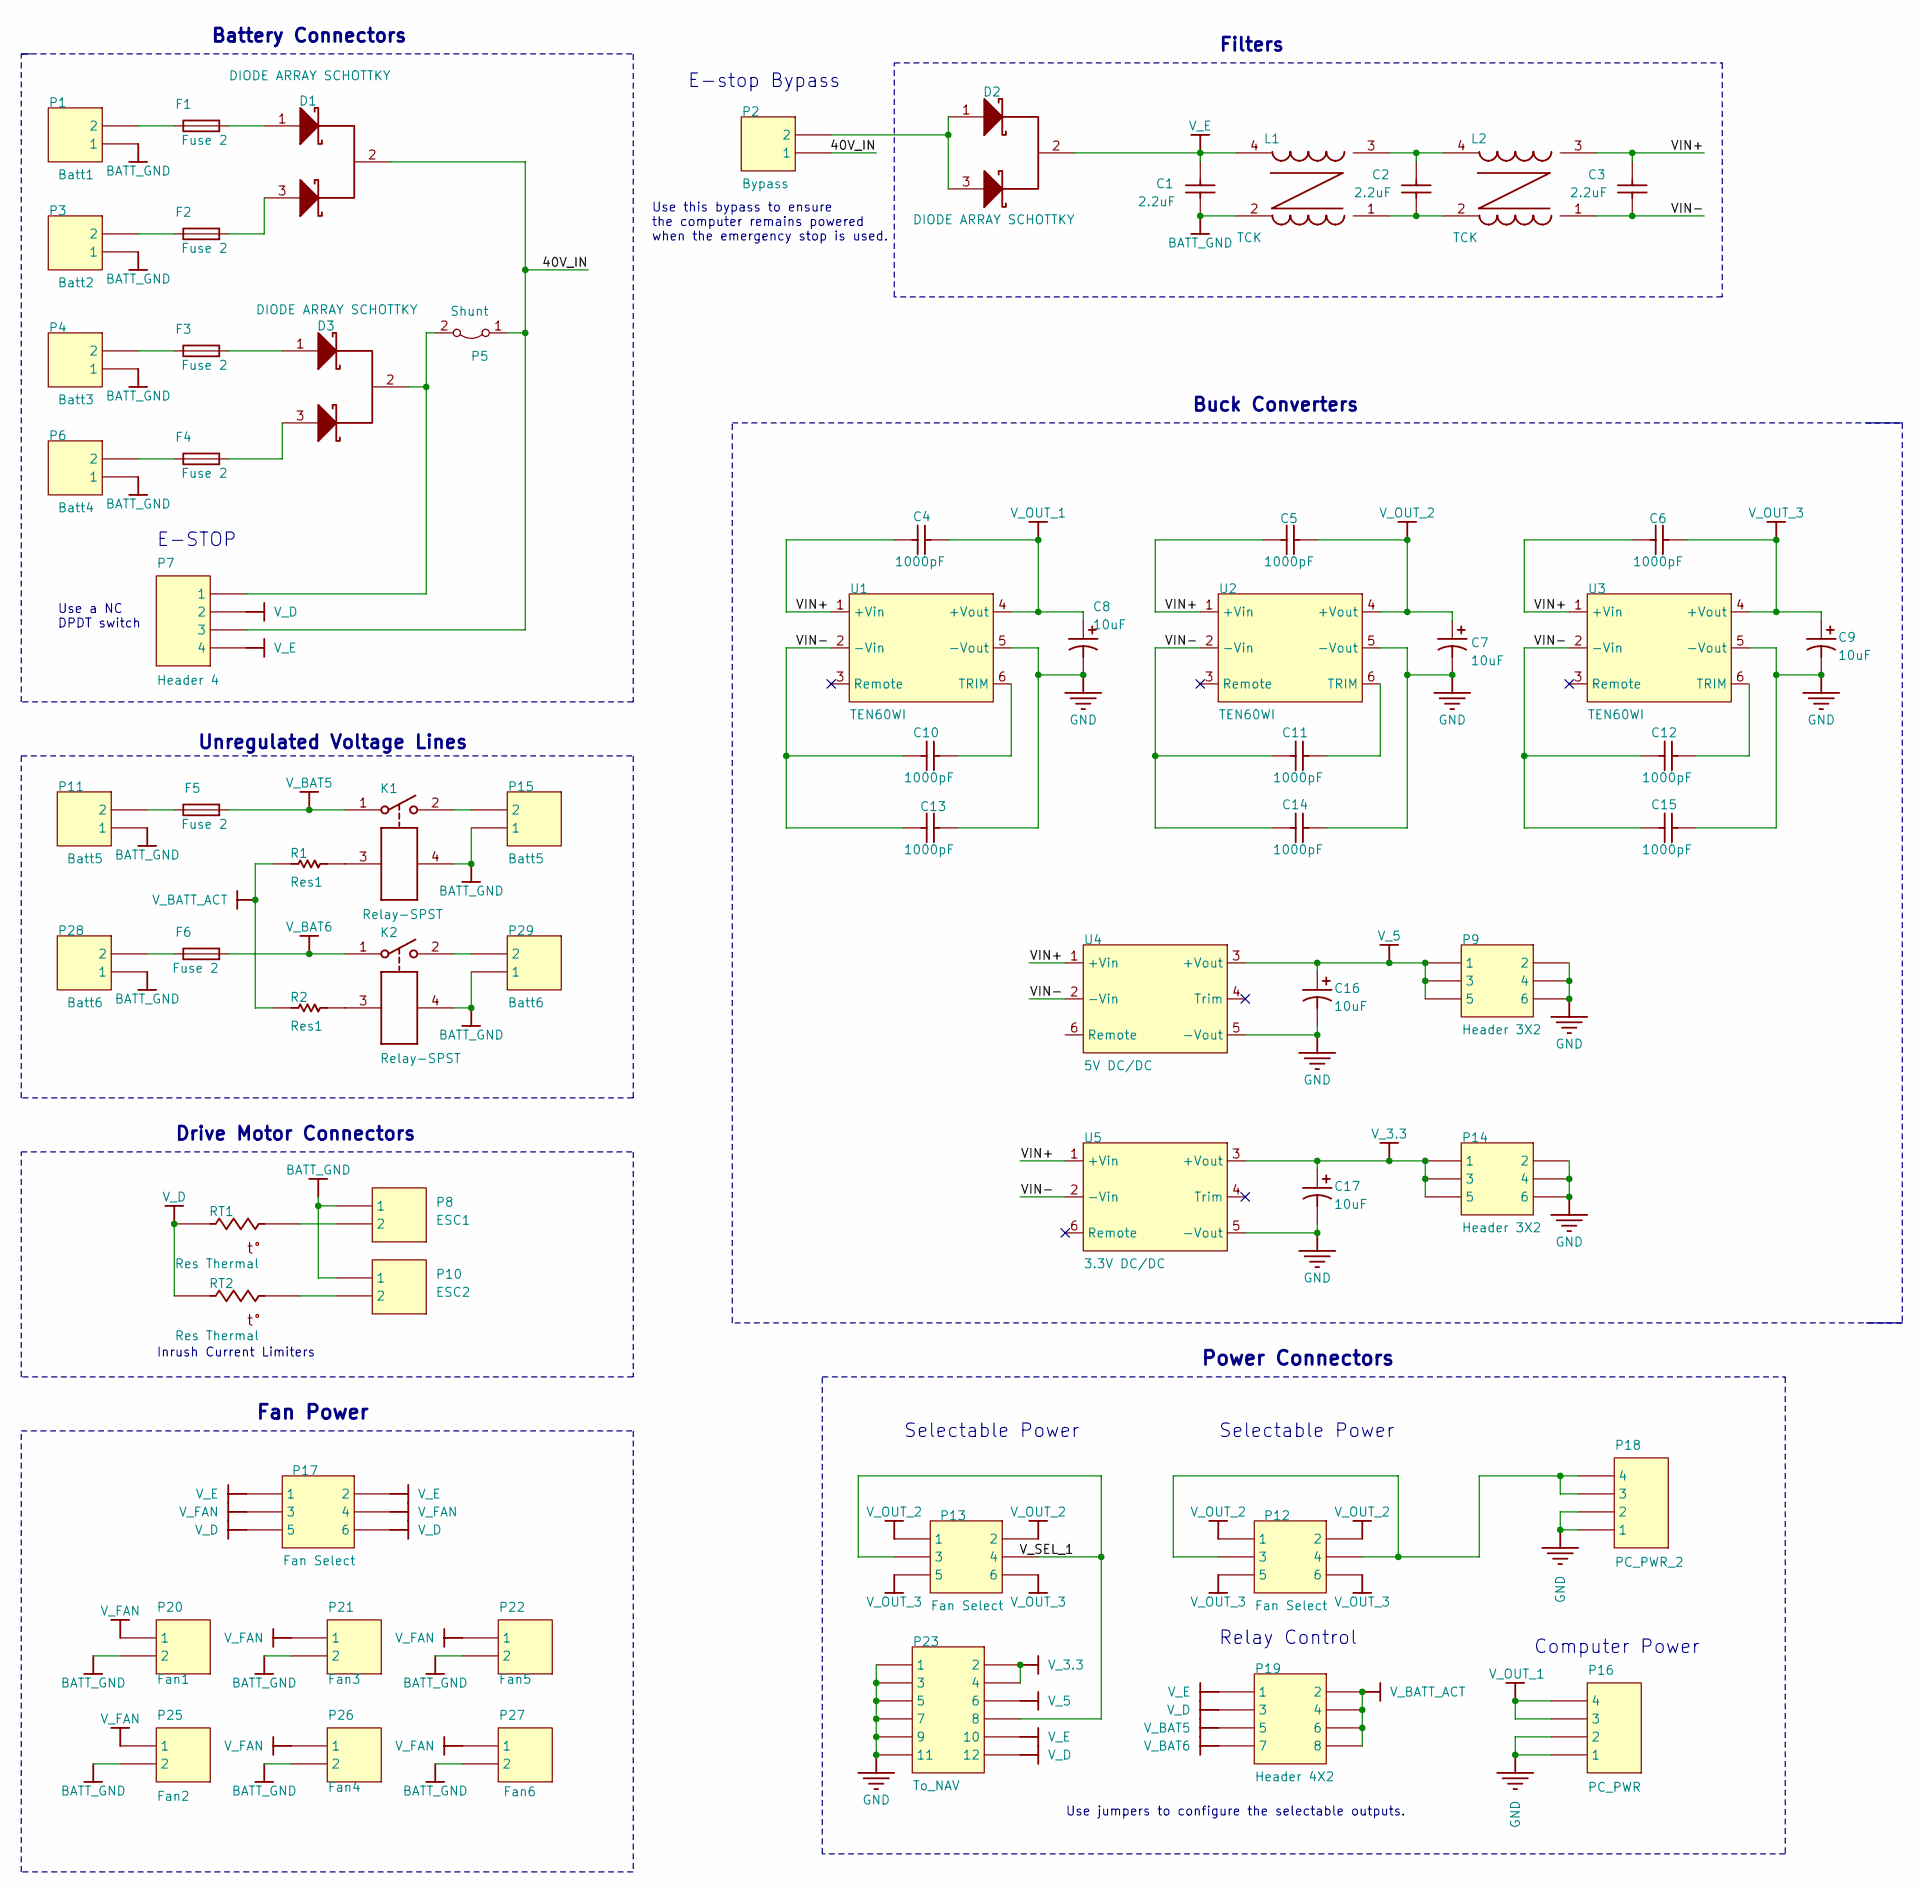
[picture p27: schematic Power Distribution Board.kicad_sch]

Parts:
C1, C2, C3: 2.2uF; SMD Cap
C4, C5, C6, C10, C11, C12, C13, C14, C15: 1000pF; SMD Cap
C7, C8, C9, C16, C17: 10uF; SMD Cap Pol
D1, D2, D3: DIODE ARRAY SCHOTTKY; D2PAK3; Part Number MBRB20200CTT4G
F1, F2, F3, F4, F5, F6: Fuse 2; FuseHolder_2; Part Number 3568
K1, K2: Relay-SPST; Relay Socket; Part Number JW1-PS and JW1FSN-DC48V
L1: TCK; TCK Choke; Part Number TCK-053
L2: TCK; TCK Choke; Part Number TCK-076
P1: Batt1; MEGAFIT 2 RA; Part Number 1720641002
P2: Bypass; MEGAFIT 2 RA; Part Number 1720641002
P3: Batt2; MEGAFIT 2 RA; Part Number 1720641002
P4: Batt3; MEGAFIT 2 RA; Part Number 1720641002
P5: Shunt
P6: Batt4; MEGAFIT 2 RA; Part Number 1720641002
P7: Header 4; MEGAFIT 4 RA; Part Number 768250004
P8: ESC1; MEGAFIT 2 RA; Part Number 1720641002
P9, P14: Header 3X2; HDR2X3
P10: ESC2; MEGAFIT 2 RA; Part Number 1720641002
P11, P15: Batt5; MEGAFIT 2 RA; Part Number 1720641002
P12, P13, P17: Fan Select; HDR2X3
P16: PC_PWR; Minifit 4 RA; Part Number 26013115
P18: PC_PWR_2; Minifit 4 RA; Part Number 26013115
P19: Header 4X2; HDR2X4
P20: Fan1; 2 Pin Locking Shrouded Connector; Part Number 705430036
P21: Fan3; 2 Pin Locking Shrouded Connector; Part Number 705430036
P22: Fan5; 2 Pin Locking Shrouded Connector; Part Number 705430036
P23: To_NAV; Microfit 8; Part Number 430451200
P25: Fan2; 2 Pin Locking Shrouded Connector; Part Number 705430036
P26: Fan4; 2 Pin Locking Shrouded Connector; Part Number 705430036
P27: Fan6; 2 Pin Locking Shrouded Connector; Part Number 705430036
P28, P29: Batt6; MEGAFIT 2 RA; Part Number 1720641002
R1, R2: Res1; AXIAL-0.3
RT1, RT2: Res Thermal; ICL; Part Number SL12 1R010
U1, U2, U3: TEN60WI; TEN 60WIN; Part Number TEN 60-4812WIN, TEN 40-1213E, or TEN 60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
U4: 5V DC/DC; THN 20WI; Part Number THN 30-4811WI
U5: 3.3V DC/DC; THN 20WI; Part Number THN 30-4810WI

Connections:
/40V_IN: D1.2 (A), P2.1, P5.1 (A), P7.3
/VIN+: C3.1, C4.2, C5.2, C6.2, L2.3 (1), U1.1 (+Vin), U2.1 (+Vin), U3.1 (+Vin), U4.1 (+Vin), U5.1 (+Vin)
/VIN-: C3.2, C10.2, C11.2, C12.2, C13.2, C14.2, C15.2, L2.1, U1.2 (-Vin), U2.2 (-Vin), U3.2 (-Vin), U4.2 (-Vin), U5.2 (-Vin)
/V_SEL_1: P13.3, P13.4, P23.8
BATT_GND: C1.2, K1.4, K2.4, L1.2, P1.1, P3.1, P4.1, P6.1, P8.1, P10.1, P11.1, P15.1, P20.2, P21.2, P22.2, P25.2, P26.2, P27.2, P28.1, P29.1
GND: C7.2, C8.2, C9.2, C13.1, C14.1, C15.1, C16.2, C17.2, P9.2, P9.4, P9.6, P14.2, P14.4, P14.6, P16.1, P16.2, P18.1, P18.2, P23.1, P23.3, P23.5, P23.7, P23.9, P23.11, U1.5 (-Vout), U2.5 (-Vout), U3.5 (-Vout), U4.5 (-Vout), U5.5 (-Vout)
unnamed: C2.1, L1.3 (1), L2.4 (2)
unnamed: C2.2, L1.1, L2.2
unnamed: D1.1 (A), F1.2
unnamed: D1.3 (A), F2.2
unnamed: D2.1 (A), D2.3 (A), P2.2
unnamed: D3.1 (A), F3.2
unnamed: D3.3 (A), F4.2
unnamed: F1.1, P1.2
unnamed: F2.1, P3.2
unnamed: F3.1, P4.2
unnamed: F4.1, P6.2
unnamed: F5.1, P11.2
unnamed: F6.1, P28.2
unnamed: K1.2, P15.2
unnamed: K1.3, R1.2
unnamed: K2.2, P29.2
unnamed: K2.3, R2.2
unnamed: D3.2 (A), P5.2 (B), P7.1
unnamed: P8.2, RT1.1
unnamed: P10.2, RT2.1
unnamed: P12.3, P12.4, P18.3, P18.4
unnamed: C10.1, U1.6 (TRIM)
unnamed: C11.1, U2.6 (TRIM)
unnamed: C12.1, U3.6 (TRIM)
V_3.3: C17.1, P14.1, P14.3, P14.5, P23.2, P23.4, U5.3 (+Vout)
V_5: C16.1, P9.1, P9.3, P9.5, P23.6, U4.3 (+Vout)
V_BAT5: F5.2, K1.1, P19.5
V_BAT6: F6.2, K2.1, P19.7
V_BATT_ACT: P19.2, P19.4, P19.6, P19.8, R1.1, R2.1
V_D: P7.2, P17.5, P17.6, P19.3, P23.12, RT1.2, RT2.2
V_E: C1.1, D2.2 (A), L1.4 (2), P7.4, P17.1, P17.2, P19.1, P23.10
V_FAN: P17.3, P17.4, P20.1, P21.1, P22.1, P25.1, P26.1, P27.1
V_OUT_1: C4.1, C8.1, P16.3, P16.4, U1.4 (+Vout)
V_OUT_2: C5.1, C7.1, P12.1, P12.2, P13.1, P13.2, U2.4 (+Vout)
V_OUT_3: C6.1, C9.1, P12.5, P12.6, P13.5, P13.6, U3.4 (+Vout)

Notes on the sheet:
Filters
Use this bypass to ensure the computer remains powered when the emergency stop is used.
Relay Control
Selectable Power
Unregulated Voltage Lines
Buck Converters
Inrush Current Limiters
E-STOP
Use jumpers to configure the selectable outputs.
Drive Motor Connectors
E-stop Bypass
Fan Power
Power Connectors
Use a NC DPDT switch
Battery Connectors
Computer Power

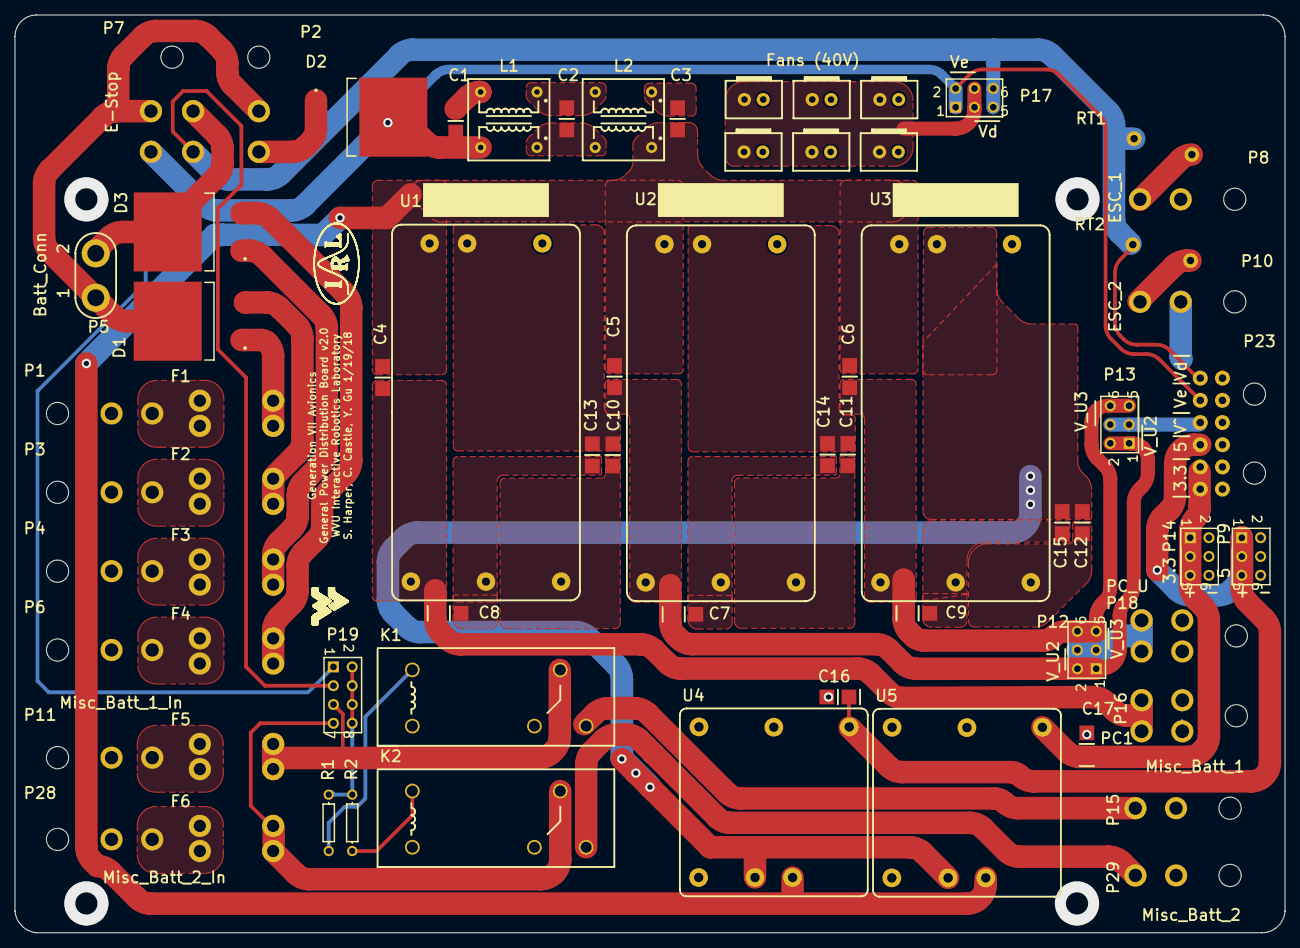
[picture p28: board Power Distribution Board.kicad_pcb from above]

Board: 2 copper layers, 171.7 x 124.1 mm, 67 parts (0 on the bottom side), 41 nets.

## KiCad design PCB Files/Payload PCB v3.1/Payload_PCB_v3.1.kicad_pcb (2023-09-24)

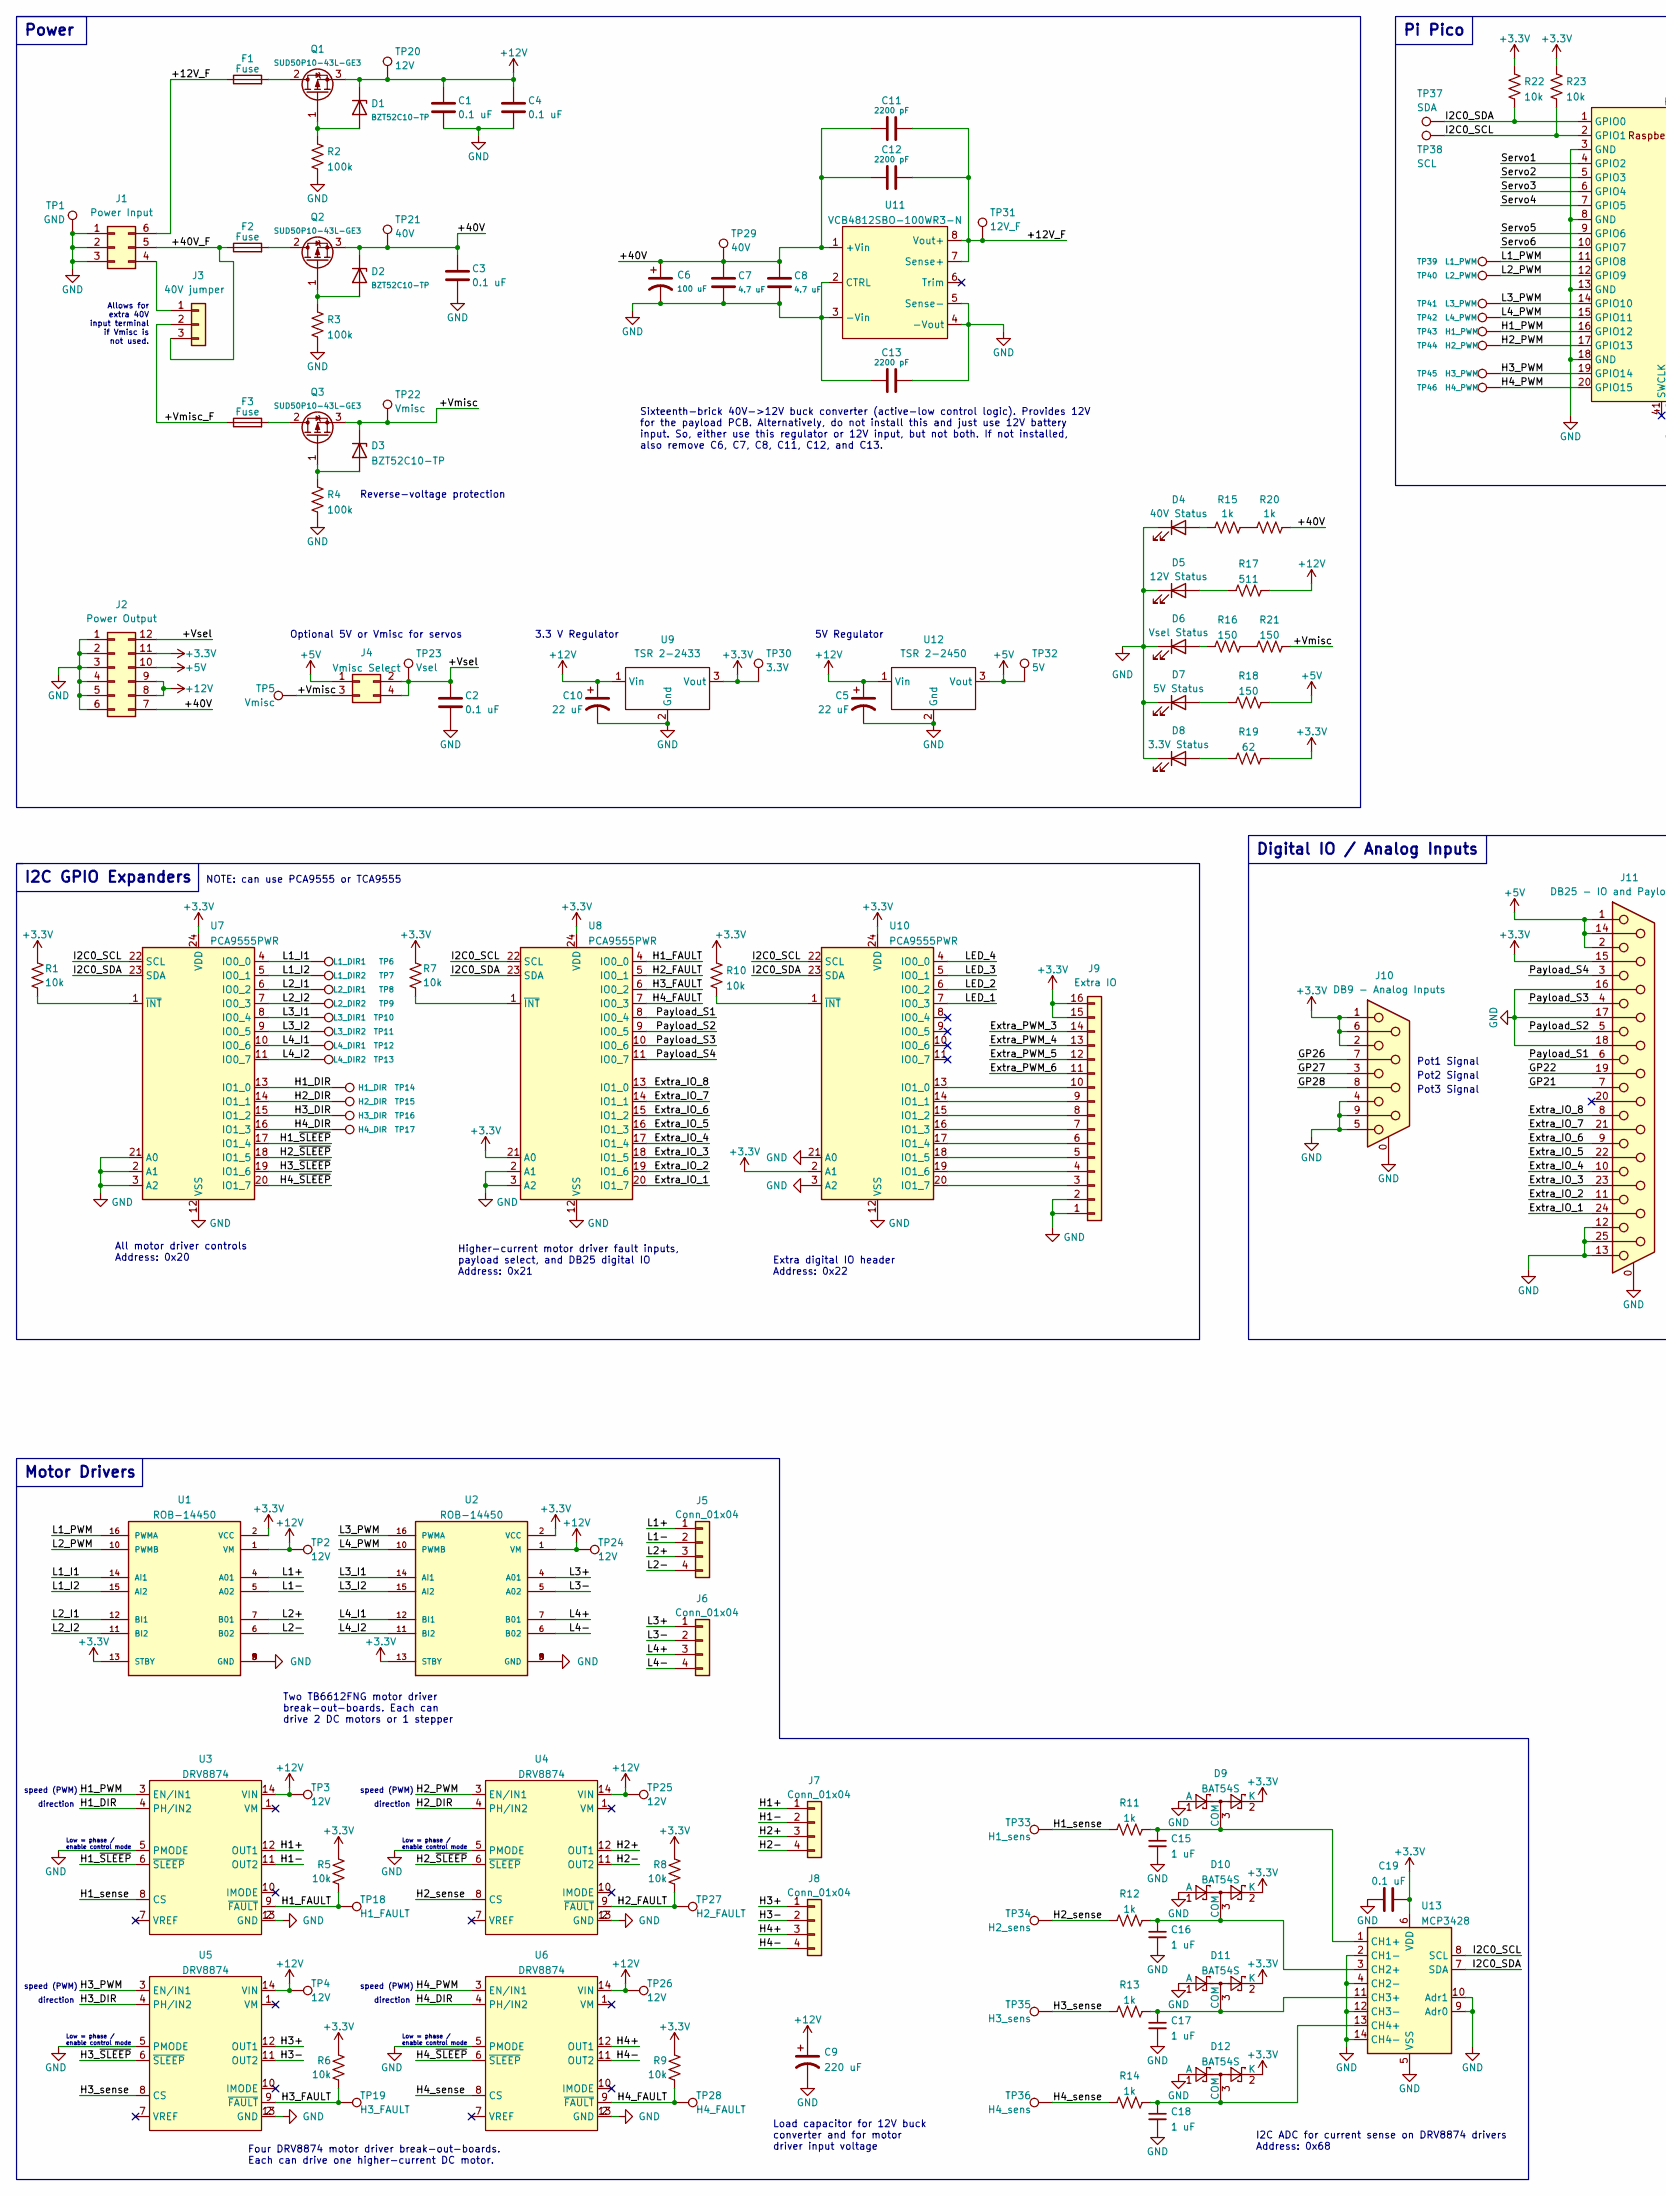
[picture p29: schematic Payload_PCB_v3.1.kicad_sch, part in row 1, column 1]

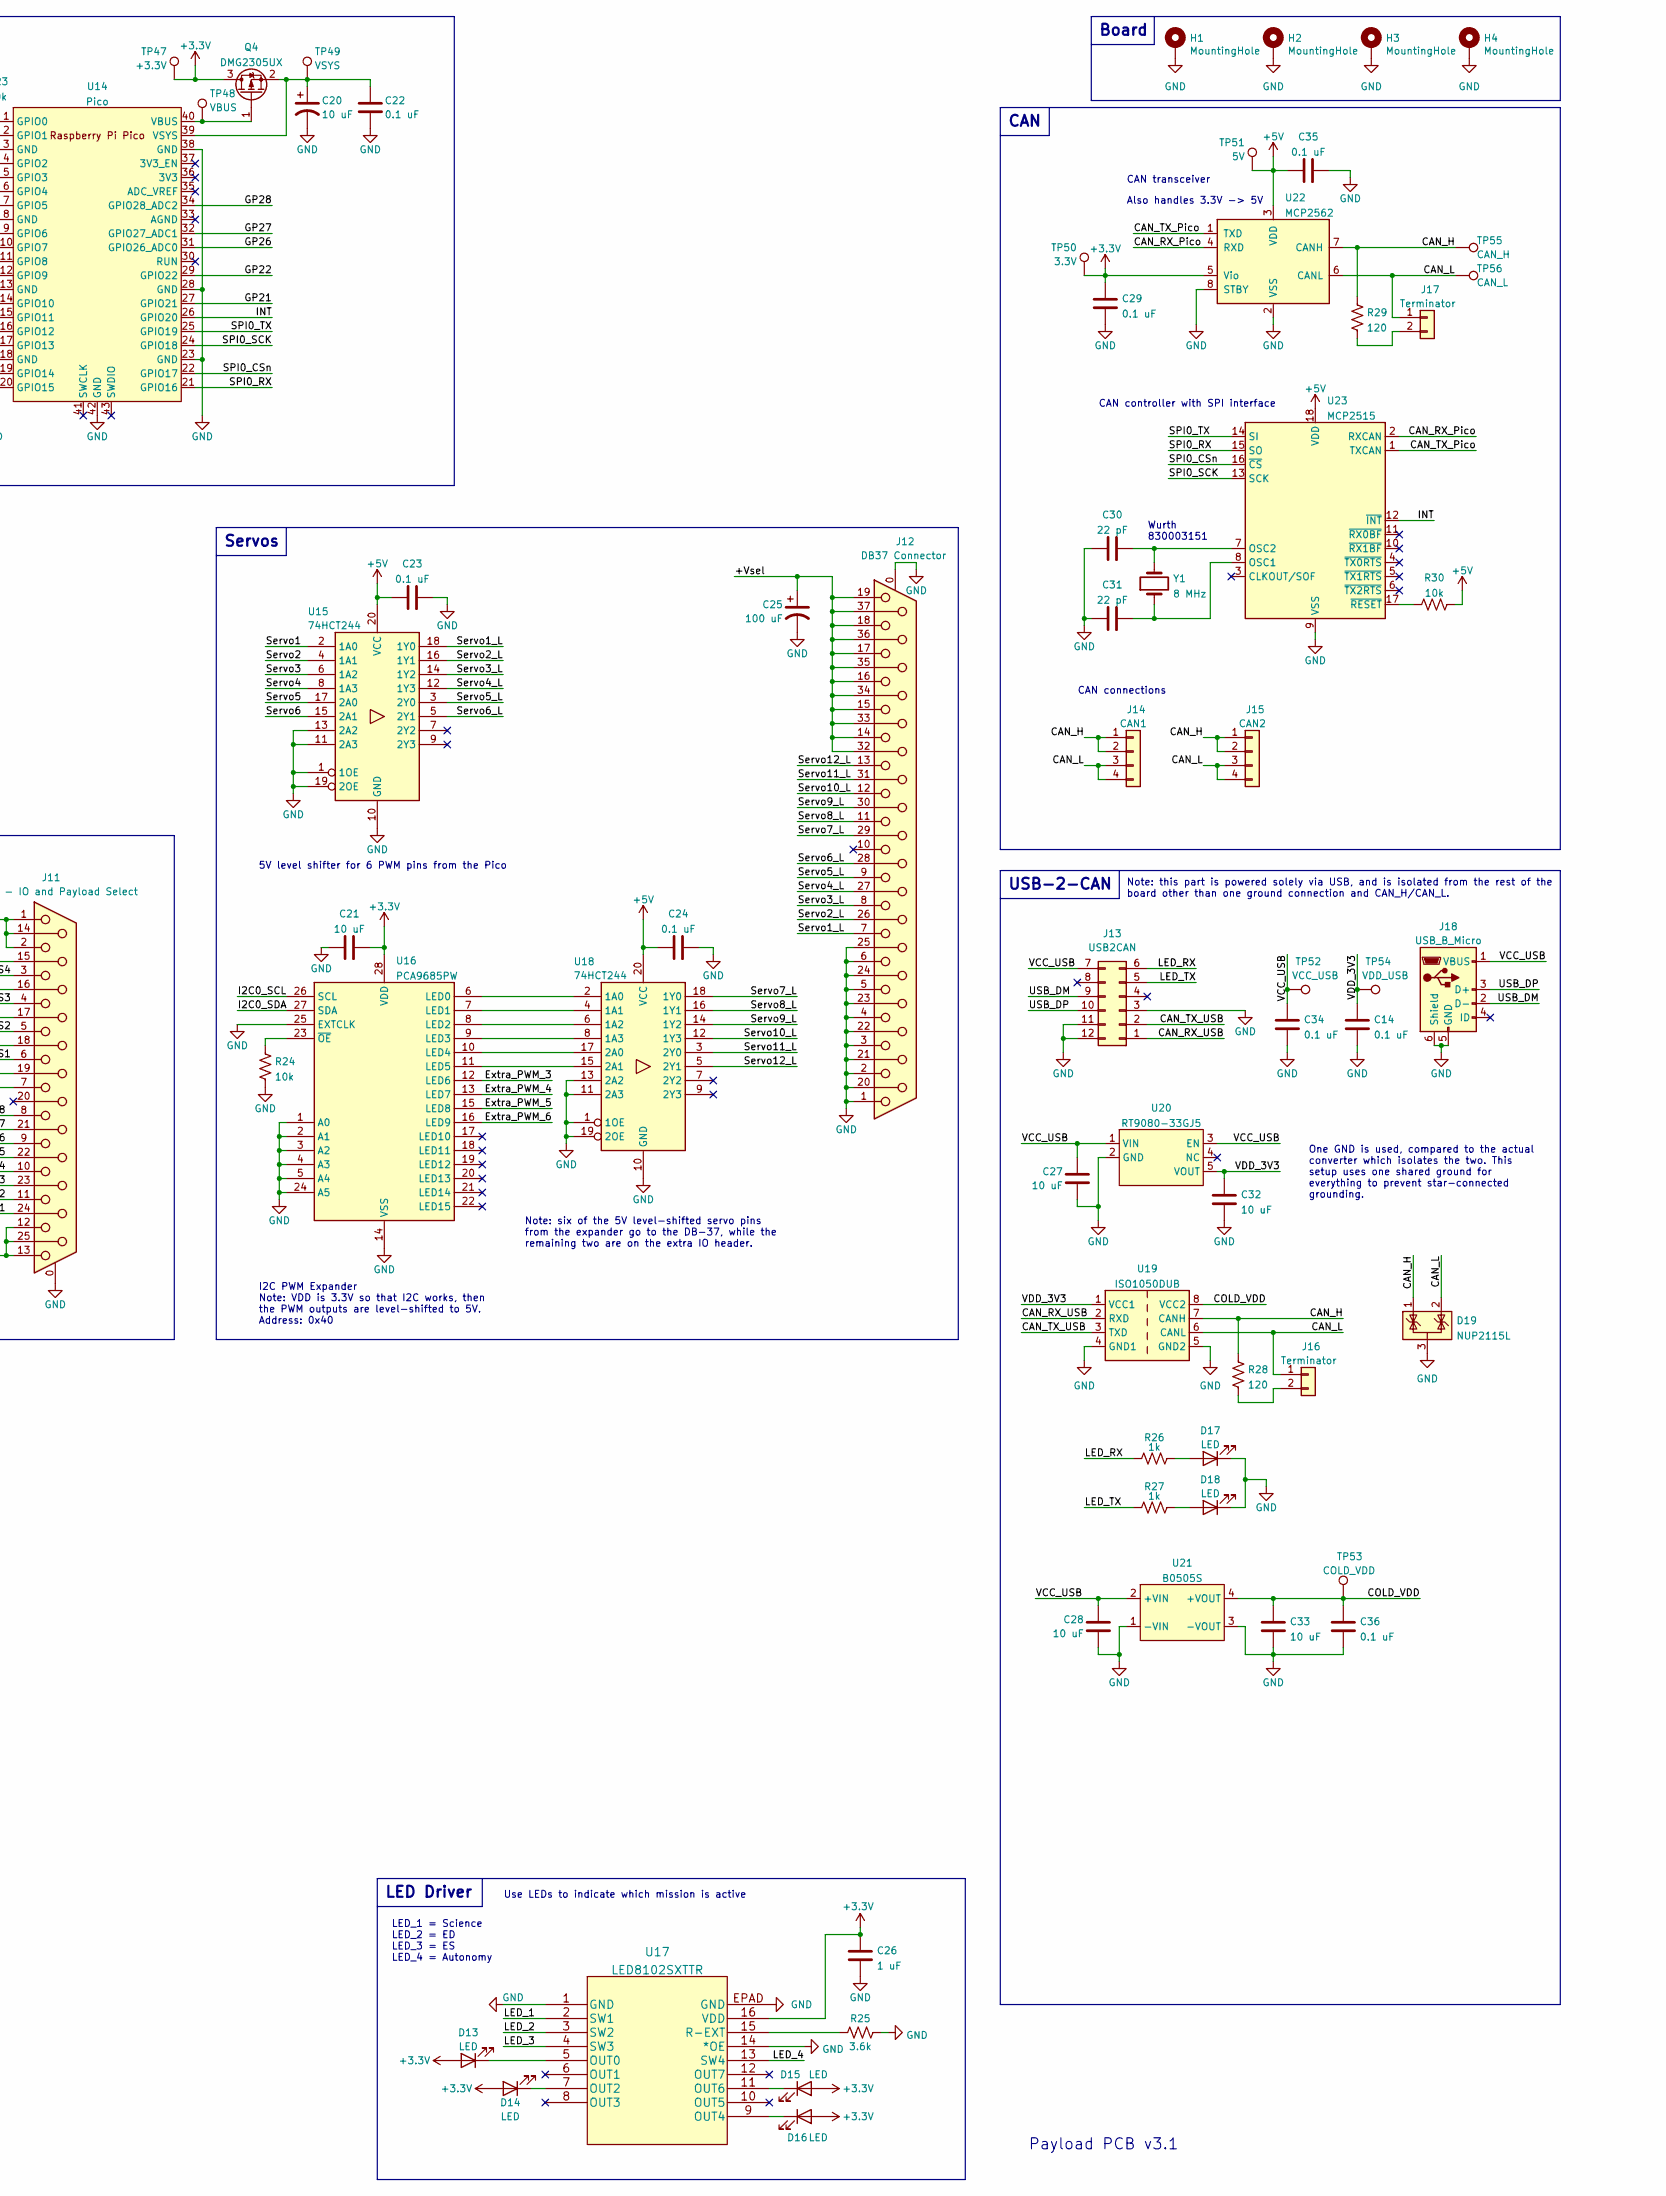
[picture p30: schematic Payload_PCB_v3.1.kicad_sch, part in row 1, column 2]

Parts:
C1, C2, C3, C4, C14, C19, C22, C23, C24, C29, C34, C35, C36: 0.1 uF; C_1206_3216Metric_Pad1.33x1.80mm_HandSolder
C5, C10: 22 uF; UCM1H220MCL1GS
C6, C25: 100 uF; CP_Radial_D10.0mm_P5.00mm
C7, C8: 4.7 uF; C_1206_3216Metric_Pad1.33x1.80mm_HandSolder
C9: 220 uF; CP_Radial_D10.0mm_P5.00mm
C11, C12, C13: 2200 pF; C_1206_3216Metric_Pad1.33x1.80mm_HandSolder
C15, C16, C17, C18, C26: 1 uF; C_1206_3216Metric_Pad1.33x1.80mm_HandSolder
C20: 10 uF; UCM1H220MCL1GS
C21, C27, C28, C32, C33: 10 uF; C_1206_3216Metric_Pad1.33x1.80mm_HandSolder
C30, C31: 22 pF; C_0603_1608Metric_Pad1.08x0.95mm_HandSolder
D1, D2, D3: BZT52C10-TP; D_SOD-123
D4: 40V Status; LED_0805_2012Metric_Pad1.15x1.40mm_HandSolder
D5: 12V Status; LED_0805_2012Metric_Pad1.15x1.40mm_HandSolder
D6: Vsel Status; LED_0805_2012Metric_Pad1.15x1.40mm_HandSolder
D7: 5V Status; LED_0805_2012Metric_Pad1.15x1.40mm_HandSolder
D8: 3.3V Status; LED_0805_2012Metric_Pad1.15x1.40mm_HandSolder
D9, D10, D11, D12: BAT54S; SOT-23
D13, D14, D15, D16, D17, D18: LED; LED_0805_2012Metric_Pad1.15x1.40mm_HandSolder
D19: NUP2115L; SOT-23
F1, F2, F3: Fuse; Fuseholder_Blade_Mini_Keystone_3568
H1, H2, H3, H4: MountingHole; MountingHole_3.2mm_M3_DIN965_Pad
J1: Power Input; Molex_Mini-Fit_Jr_5569-06A2_2x03_P4.20mm_Horizontal
J2: Power Output; Molex_Mini-Fit_Jr_5569-12A2_2x06_P4.20mm_Horizontal
J3: 40V jumper; 3_Wire_Jumper
J4: Vmisc Select; PinHeader_2x02_P2.54mm_Vertical
J5, J6, J7, J8: Conn_01x04; PhoenixContact_MCV_1,5_4-G-3.5_1x04_P3.50mm_Vertical
J9: Extra IO; PinSocket_2x08_P2.54mm_Vertical
J10: DB9 - Analog Inputs; DSUB-9_Female_Vertical_P2.77x2.84mm_MountingHoles
J11: DB25 - IO and Payload Select; DSUB-25_Female_Vertical_P2.77x2.84mm_MountingHoles
J12: DB37 Connector; DSUB-37_Female_Vertical_P2.77x2.84mm_MountingHoles
J13: USB2CAN; USB_2_CAN_Headers
J14: CAN1; 2604-3102
J15: CAN2; 2604-3102
J16, J17: Terminator; PinHeader_1x02_P2.54mm_Vertical
J18: USB_B_Micro; USB_Micro-B_Molex-105017-0001
Q1, Q2, Q3: SUD50P10-43L-GE3; TO-252-2
Q4: DMG2305UX; SOT-23
R1, R5, R6, R7, R8, R9, R10, R22, R23, R24, R30: 10k; R_0805_2012Metric_Pad1.20x1.40mm_HandSolder
R2, R3, R4: 100k; R_0805_2012Metric_Pad1.20x1.40mm_HandSolder
R11, R12, R13, R14, R15, R20, R26, R27: 1k; R_0805_2012Metric_Pad1.20x1.40mm_HandSolder
R16, R18, R21: 150; R_0805_2012Metric_Pad1.20x1.40mm_HandSolder
R17: 511; R_0805_2012Metric_Pad1.20x1.40mm_HandSolder
R19: 62; R_0805_2012Metric_Pad1.20x1.40mm_HandSolder
R25: 3.6k; R_0805_2012Metric_Pad1.20x1.40mm_HandSolder
R28, R29: 120; R_0805_2012Metric_Pad1.20x1.40mm_HandSolder
TP1: GND; TestPoint_THTPad_1.5x1.5mm_Drill0.7mm
TP2, TP3, TP4, TP24, TP25, TP26: 12V; TestPoint_THTPad_1.0x1.0mm_Drill0.5mm
TP5: Vmisc; TestPoint_THTPad_1.5x1.5mm_Drill0.7mm
TP6: L1_DIR1; TestPoint_Pad_1.5x1.5mm
TP7: L1_DIR2; TestPoint_Pad_1.5x1.5mm
TP8: L2_DIR1; TestPoint_Pad_1.5x1.5mm
TP9: L2_DIR2; TestPoint_Pad_1.5x1.5mm
TP10: L3_DIR1; TestPoint_Pad_1.5x1.5mm
TP11: L3_DIR2; TestPoint_Pad_1.5x1.5mm
TP12: L4_DIR1; TestPoint_Pad_1.5x1.5mm
TP13: L4_DIR2; TestPoint_Pad_1.5x1.5mm
TP14: H1_DIR; TestPoint_Pad_1.5x1.5mm
TP15: H2_DIR; TestPoint_Pad_1.5x1.5mm
TP16: H3_DIR; TestPoint_Pad_1.5x1.5mm
TP17: H4_DIR; TestPoint_Pad_1.5x1.5mm
TP18: H1_FAULT; TestPoint_Pad_1.5x1.5mm
TP19: H3_FAULT; TestPoint_Pad_1.5x1.5mm
TP20: 12V; TestPoint_Pad_1.5x1.5mm
TP21: 40V; TestPoint_Pad_1.5x1.5mm
TP22: Vmisc; TestPoint_Pad_1.5x1.5mm
TP23: Vsel; TestPoint_THTPad_1.5x1.5mm_Drill0.7mm
TP27: H2_FAULT; TestPoint_Pad_1.5x1.5mm
TP28: H4_FAULT; TestPoint_Pad_1.5x1.5mm
TP29: 40V; TestPoint_THTPad_1.5x1.5mm_Drill0.7mm
TP30, TP50: 3.3V; TestPoint_THTPad_1.5x1.5mm_Drill0.7mm
TP31: 12V_F; TestPoint_THTPad_1.5x1.5mm_Drill0.7mm
TP32, TP51: 5V; TestPoint_THTPad_1.5x1.5mm_Drill0.7mm
TP33: H1_sens; TestPoint_Pad_1.5x1.5mm
TP34: H2_sens; TestPoint_Pad_1.5x1.5mm
TP35: H3_sens; TestPoint_Pad_1.5x1.5mm
TP36: H4_sens; TestPoint_Pad_1.5x1.5mm
TP37: SDA; TestPoint_THTPad_1.5x1.5mm_Drill0.7mm
TP38: SCL; TestPoint_THTPad_1.5x1.5mm_Drill0.7mm
TP39: L1_PWM; TestPoint_Pad_1.5x1.5mm
TP40: L2_PWM; TestPoint_Pad_1.5x1.5mm
TP41: L3_PWM; TestPoint_Pad_1.5x1.5mm
TP42: L4_PWM; TestPoint_Pad_1.5x1.5mm
TP43: H1_PWM; TestPoint_Pad_1.5x1.5mm
TP44: H2_PWM; TestPoint_Pad_1.5x1.5mm
TP45: H3_PWM; TestPoint_Pad_1.5x1.5mm
TP46: H4_PWM; TestPoint_Pad_1.5x1.5mm
TP47: +3.3V; TestPoint_THTPad_1.5x1.5mm_Drill0.7mm
TP48: VBUS; TestPoint_THTPad_1.5x1.5mm_Drill0.7mm
TP49: VSYS; TestPoint_THTPad_1.5x1.5mm_Drill0.7mm
TP52: VCC_USB; TestPoint_THTPad_1.5x1.5mm_Drill0.7mm
TP53: COLD_VDD; TestPoint_THTPad_1.5x1.5mm_Drill0.7mm
TP54: VDD_USB; TestPoint_THTPad_1.5x1.5mm_Drill0.7mm
TP55: CAN_H; TestPoint_THTPad_1.5x1.5mm_Drill0.7mm
TP56: CAN_L; TestPoint_THTPad_1.5x1.5mm_Drill0.7mm
U1, U2: ROB-14450; MODULE_ROB-14450; PARTREV 11-13-17
U3, U4, U5, U6: DRV8874
U7, U8, U10: PCA9555PWR; TSSOP-24_4.4x7.8mm_P0.65mm
U9: TSR 2-2433; CONV_TSR_2-2433
U11: VCB4812SBO-100WR3-N; VCB4812SBO-100WFR3-N
U12: TSR 2-2450; CONV_TSR_2-2433
U13: MCP3428; SOIC-14_3.9x8.7mm_P1.27mm
U14: Pico; RPi_Pico_SMD_TH
U15, U18: 74HCT244; SO-20_12.8x7.5mm_P1.27mm
U16: PCA9685PW; TSSOP-28_4.4x9.7mm_P0.65mm
U17: LED8102SXTTR
U19: ISO1050DUB; SOP-8_6.62x9.15mm_P2.54mm
U20: RT9080-33GJ5; SOT-23-5_HandSoldering
U21: B0505S; CONV_B0505S-1WR3
U22: MCP2562; SOIC-8_3.9x4.9mm_P1.27mm
U23: MCP2515; SOIC-18W_7.5x11.6mm_P1.27mm
Y1: 8 MHz; Crystal_SMD_HC49-SD

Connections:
+3V3: C19.2, C21.2, C26.1, C29.1, D9.2 (K), D10.2 (K), D11.2 (K), D12.2 (K), D13.2 (A), D14.2 (A), D15.2 (A), D16.2 (A), J2.11, J9.15, J9.16, J10.1, J10.2, J10.6, J11.15, Q4.3 (D), R1.2, R5.1, R6.1, R7.2, R8.1, R9.1, R10.2, R19.2, R22.2, R23.2, TP30.1, TP47.1, TP50.1, U1.2 (VCC), U1.13 (STBY), U2.2 (VCC), U2.13 (STBY), U7.24 (VDD), U8.21 (A0), U8.24 (VDD), U9.3 (Vout), U10.2 (A1), U10.24 (VDD), U13.6 (VDD), U16.28 (VDD), U17.16 (VDD), U22.5 (Vio)
+5V: C23.1, C24.1, C35.1, J2.10, J4.1, J11.1, J11.2, J11.14, R18.2, R30.2, TP32.1, TP51.1, U12.3 (Vout), U15.20 (VCC), U18.20 (VCC), U22.3 (VDD), U23.18 (VDD)
+12V: C1.2, C4.2, C5.1, C9.1, C10.1, D1.1 (K), J2.8, J2.9, Q1.3 (S), R17.2, TP2.1, TP3.1, TP4.1, TP20.1, TP24.1, TP25.1, TP26.1, U1.1 (VM), U2.1 (VM), U3.14 (VIN), U4.14 (VIN), U5.14 (VIN), U6.14 (VIN), U9.1 (Vin), U12.1 (Vin)
/+12V_F: C11.2, C12.2, F1.1, J1.6, TP31.1, U11.7 (Sense+), U11.8 (Vout+)
/+40V: C3.2, C6.1, C7.1, C8.1, C11.1, C12.1, D2.1 (K), J2.7, Q2.3 (S), R20.2, TP21.1, TP29.1, U11.1 (+Vin)
/+40V_F: F2.1, J1.5, J3.3
/+Vmisc: D3.1 (K), J4.3, Q3.3 (S), R21.2, TP5.1, TP22.1
/+Vmisc_F: F3.1, J3.2
/+Vsel: C2.2, C25.1, J2.12, J4.2, J4.4, J12.14, J12.15, J12.16, J12.17, J12.18, J12.19, J12.32, J12.33, J12.34, J12.35, J12.36, J12.37, TP23.1
/CAN_H: D19.1 (K), J14.1, J14.2, J15.1, J15.2, R28.2, R29.2, TP55.1, U19.7 (CANH), U22.7 (CANH)
/CAN_L: D19.2 (K), J14.3, J14.4, J15.3, J15.4, J16.1, J17.1, TP56.1, U19.6 (CANL), U22.6 (CANL)
/CAN_RX_Pico: U22.4 (RXD), U23.2 (RXCAN)
/CAN_RX_USB: J13.1, U19.2 (RXD)
/CAN_TX_Pico: U22.1 (TXD), U23.1 (TXCAN)
/CAN_TX_USB: J13.2, U19.3 (TXD)
/COLD_VDD: C33.1, C36.1, TP53.1, U19.8 (VCC2), U21.4 (+VOUT)
/Extra_IO_1: J11.24, U8.20 (IO1_7)
/Extra_IO_2: J11.11, U8.19 (IO1_6)
/Extra_IO_3: J11.23, U8.18 (IO1_5)
/Extra_IO_4: J11.10, U8.17 (IO1_4)
/Extra_IO_5: J11.22, U8.16 (IO1_3)
/Extra_IO_6: J11.9, U8.15 (IO1_2)
/Extra_IO_7: J11.21, U8.14 (IO1_1)
/Extra_IO_8: J11.8, U8.13 (IO1_0)
/Extra_PWM_3: J9.14, U16.12 (LED6)
/Extra_PWM_4: J9.13, U16.13 (LED7)
/Extra_PWM_5: J9.12, U16.15 (LED8)
/Extra_PWM_6: J9.11, U16.16 (LED9)
/GP21: J11.7, U14.27 (GPIO21)
/GP22: J11.19, U14.29 (GPIO22)
/GP26: J10.7, U14.31 (GPIO26_ADC0)
/GP27: J10.3, U14.32 (GPIO27_ADC1)
/GP28: J10.8, U14.34 (GPIO28_ADC2)
/H1+: J7.1, U3.12 (OUT1)
/H1-: J7.2, U3.11 (OUT2)
/H1_DIR: TP14.1, U3.4 (PH/IN2), U7.13 (IO1_0)
/H1_FAULT: R5.2, TP18.1, U3.9 (~FAULT), U8.4 (IO0_0)
/H1_PWM: TP43.1, U3.3 (EN/IN1), U14.16 (GPIO12)
/H1_sense: R11.1, TP33.1, U3.8 (CS)
/H1_~SLEEP: U3.6 (~SLEEP), U7.17 (IO1_4)
/H2+: J7.3, U4.12 (OUT1)
/H2-: J7.4, U4.11 (OUT2)
/H2_DIR: TP15.1, U4.4 (PH/IN2), U7.14 (IO1_1)
/H2_FAULT: R8.2, TP27.1, U4.9 (~FAULT), U8.5 (IO0_1)
/H2_PWM: TP44.1, U4.3 (EN/IN1), U14.17 (GPIO13)
/H2_sense: R12.1, TP34.1, U4.8 (CS)
/H2_~SLEEP: U4.6 (~SLEEP), U7.18 (IO1_5)
/H3+: J8.1, U5.12 (OUT1)
/H3-: J8.2, U5.11 (OUT2)
/H3_DIR: TP16.1, U5.4 (PH/IN2), U7.15 (IO1_2)
/H3_FAULT: R6.2, TP19.1, U5.9 (~FAULT), U8.6 (IO0_2)
/H3_PWM: TP45.1, U5.3 (EN/IN1), U14.19 (GPIO14)
/H3_sense: R13.1, TP35.1, U5.8 (CS)
/H3_~SLEEP: U5.6 (~SLEEP), U7.19 (IO1_6)
/H4+: J8.3, U6.12 (OUT1)
/H4-: J8.4, U6.11 (OUT2)
/H4_DIR: TP17.1, U6.4 (PH/IN2), U7.16 (IO1_3)
/H4_FAULT: R9.2, TP28.1, U6.9 (~FAULT), U8.7 (IO0_3)
/H4_PWM: TP46.1, U6.3 (EN/IN1), U14.20 (GPIO15)
/H4_sense: R14.1, TP36.1, U6.8 (CS)
/H4_~SLEEP: U6.6 (~SLEEP), U7.20 (IO1_7)
/I2C0_SCL: R23.1, TP38.1, U7.22 (SCL), U8.22 (SCL), U10.22 (SCL), U13.8 (SCL), U14.2 (GPIO1), U16.26 (SCL)
/I2C0_SDA: R22.1, TP37.1, U7.23 (SDA), U8.23 (SDA), U10.23 (SDA), U13.7 (SDA), U14.1 (GPIO0), U16.27 (SDA)
/INT: U14.26 (GPIO20), U23.12 (~INT)
/L1+: J5.1, U1.4 (A01)
/L1-: J5.2, U1.5 (A02)
/L1_I1: TP6.1, U1.14 (AI1), U7.4 (IO0_0)
/L1_I2: TP7.1, U1.15 (AI2), U7.5 (IO0_1)
/L1_PWM: TP39.1, U1.16 (PWMA), U14.11 (GPIO8)
/L2+: J5.3, U1.7 (B01)
/L2-: J5.4, U1.6 (B02)
/L2_I1: TP8.1, U1.12 (BI1), U7.6 (IO0_2)
/L2_I2: TP9.1, U1.11 (BI2), U7.7 (IO0_3)
/L2_PWM: TP40.1, U1.10 (PWMB), U14.12 (GPIO9)
/L3+: J6.1, U2.4 (A01)
/L3-: J6.2, U2.5 (A02)
/L3_I1: TP10.1, U2.14 (AI1), U7.8 (IO0_4)
/L3_I2: TP11.1, U2.15 (AI2), U7.9 (IO0_5)
/L3_PWM: TP41.1, U2.16 (PWMA), U14.14 (GPIO10)
/L4+: J6.3, U2.7 (B01)
/L4-: J6.4, U2.6 (B02)
/L4_I1: TP12.1, U2.12 (BI1), U7.10 (IO0_6)
/L4_I2: TP13.1, U2.11 (BI2), U7.11 (IO0_7)
/L4_PWM: TP42.1, U2.10 (PWMB), U14.15 (GPIO11)
/LED_1: U10.7 (IO0_3), U17.2 (SW1)
/LED_2: U10.6 (IO0_2), U17.3 (SW2)
/LED_3: U10.5 (IO0_1), U17.4 (SW3)
/LED_4: U10.4 (IO0_0), U17.13 (SW4)
/LED_RX: J13.6, R26.1
/LED_TX: J13.5, R27.1
/Payload_S1: J11.6, U8.8 (IO0_4)
/Payload_S2: J11.5, U8.9 (IO0_5)
/Payload_S3: J11.4, U8.10 (IO0_6)
/Payload_S4: J11.3, U8.11 (IO0_7)
/SPI0_CSn: U14.22 (GPIO17), U23.16 (~CS)
/SPI0_RX: U14.21 (GPIO16), U23.15 (SO)
/SPI0_SCK: U14.24 (GPIO18), U23.13 (SCK)
/SPI0_TX: U14.25 (GPIO19), U23.14 (SI)
/Servo1: U14.4 (GPIO2), U15.2 (1A0)
/Servo1_L: J12.7, U15.18 (1Y0)
/Servo2: U14.5 (GPIO3), U15.4 (1A1)
/Servo2_L: J12.26, U15.16 (1Y1)
/Servo3: U14.6 (GPIO4), U15.6 (1A2)
/Servo3_L: J12.8, U15.14 (1Y2)
/Servo4: U14.7 (GPIO5), U15.8 (1A3)
/Servo4_L: J12.27, U15.12 (1Y3)
/Servo5: U14.9 (GPIO6), U15.17 (2A0)
/Servo5_L: J12.9, U15.3 (2Y0)
/Servo6: U14.10 (GPIO7), U15.15 (2A1)
/Servo6_L: J12.28, U15.5 (2Y1)
/Servo7_L: J12.29, U18.18 (1Y0)
/Servo8_L: J12.11, U18.16 (1Y1)
/Servo9_L: J12.30, U18.14 (1Y2)
/Servo10_L: J12.12, U18.12 (1Y3)
/Servo11_L: J12.31, U18.3 (2Y0)
/Servo12_L: J12.13, U18.5 (2Y1)
/USB_DM: J13.9, J18.2 (D-)
/USB_DP: J13.10, J18.3 (D+)
/VCC_USB: C27.1, C28.1, C34.1, J13.7, J18.1 (VBUS), TP52.1, U20.1 (VIN), U20.3 (EN), U21.2 (+VIN)
/VDD_3V3: C14.1, C32.1, TP54.1, U19.1 (VCC1), U20.5 (VOUT)
GND: C1.1, C2.1, C3.1, C4.1, C5.2, C6.2, C7.2, C8.2, C9.2, C10.2, C13.1, C13.2, C14.2, C15.2, C16.2, C17.2, C18.2, C19.1, C20.2, C21.1, C22.1, C23.2, C24.2, C25.2, C26.2, C27.2, C28.2, C29.2, C30.1, C31.1, C32.2, C33.2, C34.2, C35.2, C36.2, D4.1 (K), D5.1 (K), D6.1 (K), D7.1 (K), D8.1 (K), D9.1 (A), D10.1 (A), D11.1 (A), D12.1 (A), D17.1 (K), D18.1 (K), D19.3 (A), H1.1, H2.1, H3.1, H4.1, J1.1, J1.2, J1.3, J2.1, J2.2, J2.3, J2.4, J2.5, J2.6, J9.1, J9.2, J10.0 (PAD), J10.4, J10.5, J10.9, J11.0 (PAD), J11.12, J11.13, J11.16, J11.17, J11.18, J11.25, J12.0 (PAD), J12.1, J12.2, J12.3, J12.4, J12.5, J12.6, J12.20, J12.21, J12.22, J12.23, J12.24, J12.25, J13.3, J13.11, J13.12, J18.5 (GND), J18.6 (Shield), R2.2, R3.2, R4.2, R24.1, R25.2, TP1.1, U1.3 (GND), U1.8 (GND), U1.9 (GND), U2.3 (GND), U2.8 (GND), U2.9 (GND), U3.2 (GND), U3.5 (PMODE), U3.13 (GND), U4.2 (GND), U4.5 (PMODE), U4.13 (GND), U5.2 (GND), U5.5 (PMODE), U5.13 (GND), U6.2 (GND), U6.5 (PMODE), U6.13 (GND), U7.2 (A1), U7.3 (A2), U7.12 (VSS), U7.21 (A0), U8.2 (A1), U8.3 (A2), U8.12 (VSS), U9.2 (Gnd), U10.3 (A2), U10.12 (VSS), U10.21 (A0), U11.2 (CTRL), U11.3 (-Vin), U11.4 (-Vout), U11.5 (Sense-), U12.2 (Gnd), U13.2 (CH1-), U13.4 (CH2-), U13.5 (VSS), U13.9 (Adr0), U13.10 (Adr1), U13.12 (CH3-), U13.14 (CH4-), U14.3 (GND), U14.8 (GND), U14.13 (GND), U14.18 (GND), U14.23 (GND), U14.28 (GND), U14.38 (GND), U14.42 (GND), U15.1 (1OE), U15.10 (GND), U15.11 (2A3), U15.13 (2A2), U15.19 (2OE), U16.1 (A0), U16.2 (A1), U16.3 (A2), U16.4 (A3), U16.5 (A4), U16.14 (VSS), U16.24 (A5), U16.25 (EXTCLK), U17.1 (GND), U17.14 (*OE), U17.EPAD (GND), U18.1 (1OE), U18.10 (GND), U18.11 (2A3), U18.13 (2A2), U18.19 (2OE), U19.4 (GND1), U19.5 (GND2), U20.2 (GND), U21.1 (-VIN), U21.3 (-VOUT), U22.2 (VSS), U22.8 (STBY), U23.9 (VSS)
unnamed: C15.1, D9.3 (COM), R11.2, U13.1 (CH1+)
unnamed: C16.1, D10.3 (COM), R12.2, U13.3 (CH2+)
unnamed: C17.1, D11.3 (COM), R13.2, U13.11 (CH3+)
unnamed: C18.1, D12.3 (COM), R14.2, U13.13 (CH4+)
unnamed: C20.1, C22.2, Q4.2 (S), TP49.1, U14.39 (VSYS)
unnamed: C30.2, U23.7 (OSC2), Y1.2
unnamed: C31.2, U23.8 (OSC1), Y1.1
unnamed: D1.2 (A), Q1.1 (G), R2.1
unnamed: D2.2 (A), Q2.1 (G), R3.1
unnamed: D3.2 (A), Q3.1 (G), R4.1
unnamed: D4.2 (A), R15.1
unnamed: D5.2 (A), R17.1
unnamed: D6.2 (A), R16.1
unnamed: D7.2 (A), R18.1
unnamed: D8.2 (A), R19.1
unnamed: D13.1 (K), U17.5 (OUT0)
unnamed: D14.1 (K), U17.7 (OUT2)
unnamed: D15.1 (K), U17.11 (OUT6)
unnamed: D16.1 (K), U17.9 (OUT4)
unnamed: D17.2 (A), R26.2
unnamed: D18.2 (A), R27.2
unnamed: F1.2, Q1.2 (D)
unnamed: F2.2, Q2.2 (D)
unnamed: F3.2, Q3.2 (D)
unnamed: J1.4, J3.1
unnamed: J9.3, U10.20 (IO1_7)
unnamed: J9.4, U10.19 (IO1_6)
unnamed: J9.5, U10.18 (IO1_5)
unnamed: J9.6, U10.17 (IO1_4)
unnamed: J9.7, U10.16 (IO1_3)
unnamed: J9.8, U10.15 (IO1_2)
unnamed: J9.9, U10.14 (IO1_1)
unnamed: J9.10, U10.13 (IO1_0)
unnamed: J16.2, R28.1
unnamed: J17.2, R29.1
unnamed: Q4.1 (G), TP48.1, U14.40 (VBUS)
unnamed: R1.1, U7.1 (~INT)
unnamed: R7.1, U8.1 (~INT)
unnamed: R10.1, U10.1 (~INT)
unnamed: R15.2, R20.1
unnamed: R16.2, R21.1
unnamed: R24.2, U16.23 (~OE)
unnamed: R25.1, U17.15 (R-EXT)
unnamed: R30.1, U23.17 (~RESET)
unnamed: U16.6 (LED0), U18.2 (1A0)
unnamed: U16.7 (LED1), U18.4 (1A1)
unnamed: U16.8 (LED2), U18.6 (1A2)
unnamed: U16.9 (LED3), U18.8 (1A3)
unnamed: U16.10 (LED4), U18.17 (2A0)
unnamed: U16.11 (LED5), U18.15 (2A1)

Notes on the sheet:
direction
speed (PWM)
CAN connections
Low = phase / enable control mode
Payload PCB v3.1
Two TB6612FNG motor driver break-out-boards. Each can drive 2 DC motors or 1 stepper
Allows for extra 40V input terminal if Vmisc is not used.
CAN transceiver
Sixteenth-brick 40V->12V buck converter (active-low control logic). Provides 12V for the payload PCB. Alternatively, do not install this and just use 12V battery input. So, either use this regulator or 12V input, but not both. If not installed, also remove C6, C7, C8, C11, C12, and C13.
Wurth 830003151
Pot2 Signal
Optional 5V or Vmisc for servos
5V Regulator
Board
All motor driver controls Address: 0x20
LED_1 = Science LED_2 = ED LED_3 = ES LED_4 = Autonomy
Load capacitor for 12V buck converter and for motor driver input voltage
One GND is used, compared to the actual converter which isolates the two. This setup uses one shared ground for everything to prevent star-connected grounding.
5V level shifter for 6 PWM pins from the Pico
I2C GPIO Expanders
Higher-current motor driver fault inputs, payload select, and DB25 digital IO Address: 0x21
3.3 V Regulator
Extra digital IO header Address: 0x22
CAN
Power
Pot3 Signal
Reverse-voltage protection
CAN controller with SPI interface
Note: this part is powered solely via USB, and is isolated from the rest of the board other than one ground connection and CAN_H/CAN_L.
Use LEDs to indicate which mission is active
I2C PWM Expander Note: VDD is 3.3V so that I2C works, then the PWM outputs are level-shifted to 5V. Address: 0x40
Pi Pico
USB-2-CAN
Digital IO / Analog Inputs
Note: six of the 5V level-shifted servo pins from the expander go to the DB-37, while the remaining two are on the extra IO header.
Servos
Pot1 Signal
Motor Drivers
NOTE: can use PCA9555 or TCA9555
Also handles 3.3V -> 5V

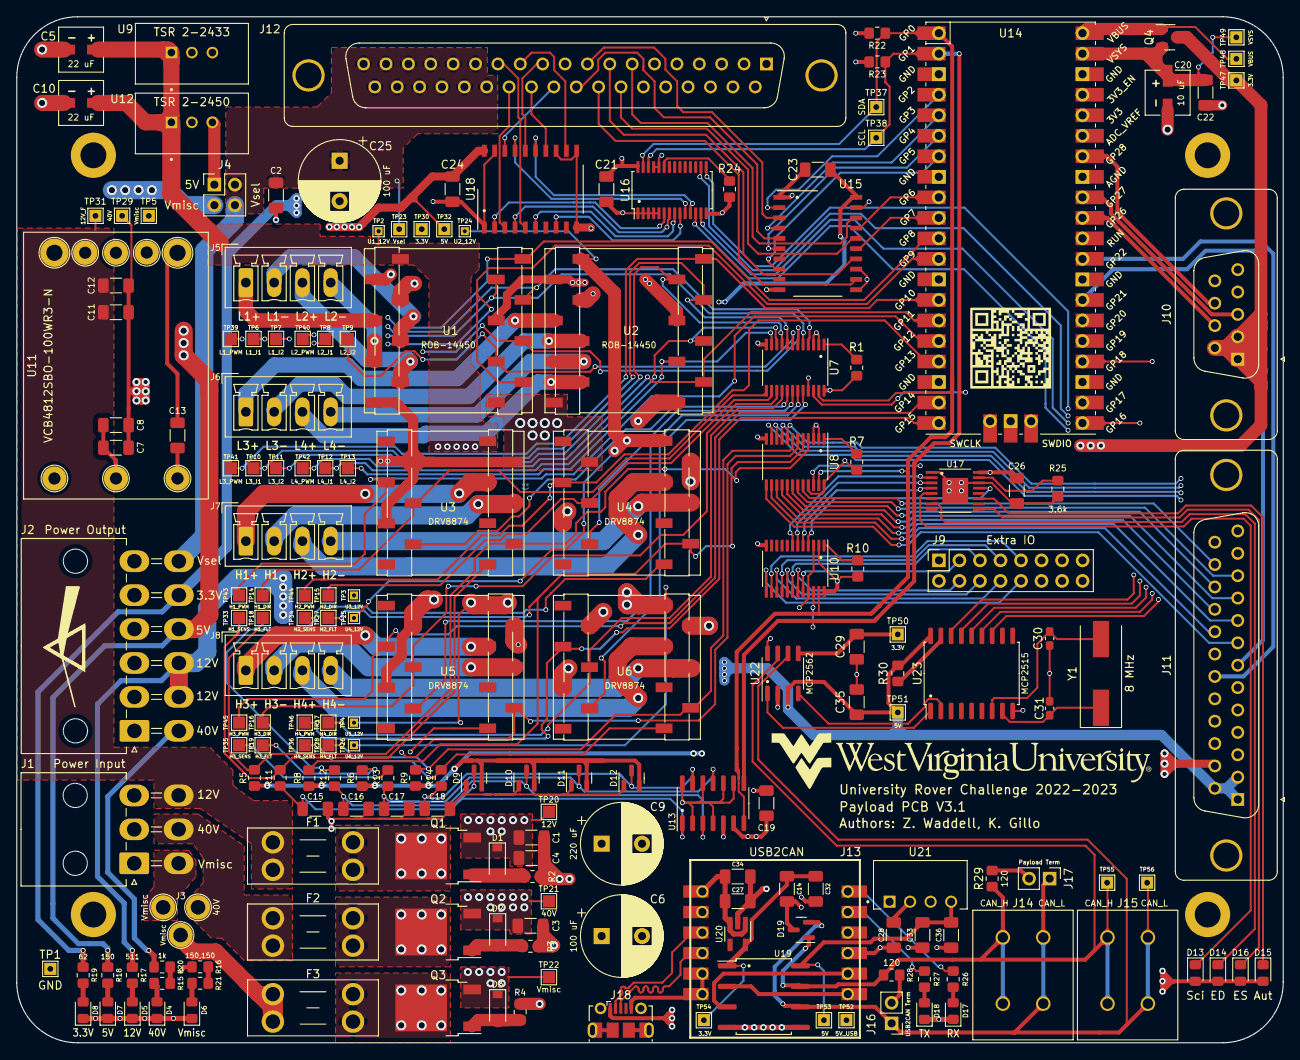
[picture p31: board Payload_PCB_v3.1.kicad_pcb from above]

Board: 4 copper layers, 156.8 x 127.0 mm, 194 parts (0 on the bottom side), 171 nets.

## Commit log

2023-09-24 Initial public release commit
    [039281103.stp, 039281123.stp, 050362296.stp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]
2023-09-24 Update README.md
    Updated readme to show battery monitor 3D rendering
2023-09-24 Update README.md
    Updated payload PCB readme to include 3D rendering

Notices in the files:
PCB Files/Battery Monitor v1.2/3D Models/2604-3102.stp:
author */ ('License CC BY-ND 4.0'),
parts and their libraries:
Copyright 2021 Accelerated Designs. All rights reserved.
